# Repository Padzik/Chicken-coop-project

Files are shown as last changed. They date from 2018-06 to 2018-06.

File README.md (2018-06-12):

# Chicken coop project ("Kurník 21. století")
Chicken coop controller board (Eagle schematics) + arduino SW (for arduino and attiny + modified dependent libraries)

## HW comment
* Arduino nano + Attiny85 (for battery protection)
* LCD with nice user friendly menu
* External temp probe + automatic fan controller
* Set your GPS location (via menu) and you are ready to go! (actual Sunrise and Sunset is automaticly calculated every day + you can add user delay time)
* Build in Buzzer for Pavlov reflex (one minute before door open/close starts beeping)
* RTC has build in automatic SW correction (cheap RTCs can be running up to 30s late every day) + automatic summer/winter time
* External LED for door status + Data output via Serial 
* H-bridge + motor from screwdriver for door opening (build in safety mechanism for sensor failure) Door position is controlled by Magnetic Sensor Window Alarm Switch (I have tried mechanical and also Hall-sensor switches, but this one is more realible)
* It has also manual override function for doors
* Solar panel / main voltage power supply + UPS 6V battery (up to 2 days of running on battery backup) + Hibernation mode for low backup voltage on battery
* Double sided PCB can be easily prepared at home conditions (I have made many prototype versions)

Inspired by [Arduino chicken project by user RobotChicken](http://www.instructables.com/id/Arduino-Chicken-Coop-Controller/)

## Photos

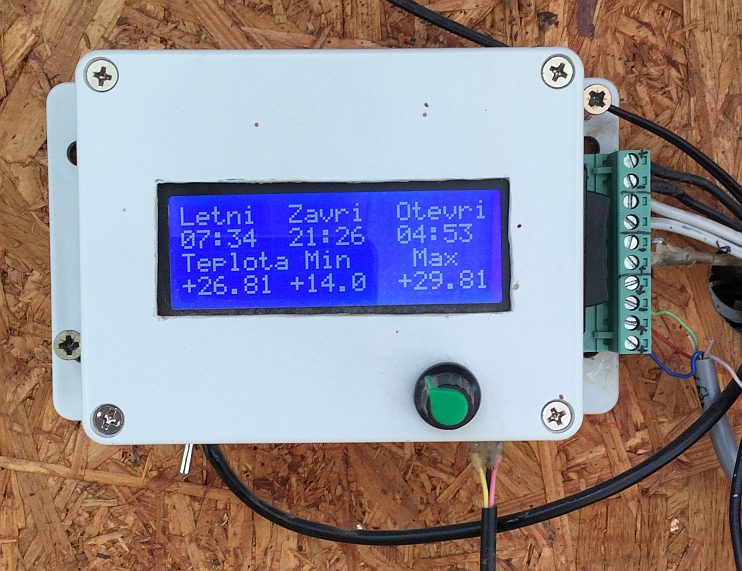
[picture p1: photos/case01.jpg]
Whole box


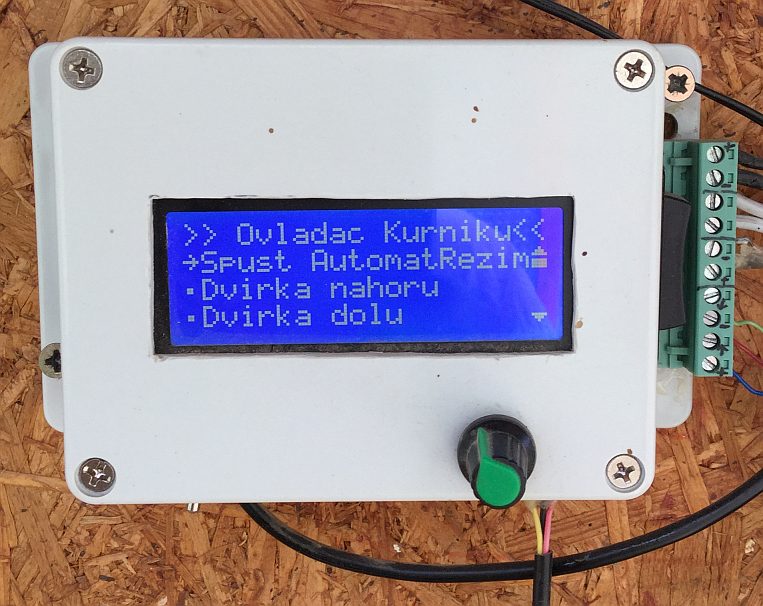
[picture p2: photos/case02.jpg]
Internal menu


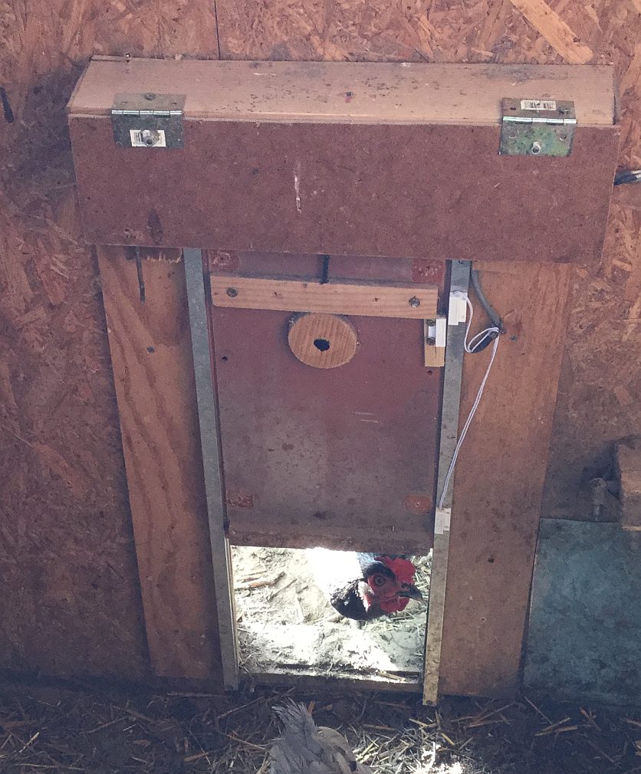
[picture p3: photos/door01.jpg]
Actual state of door HW


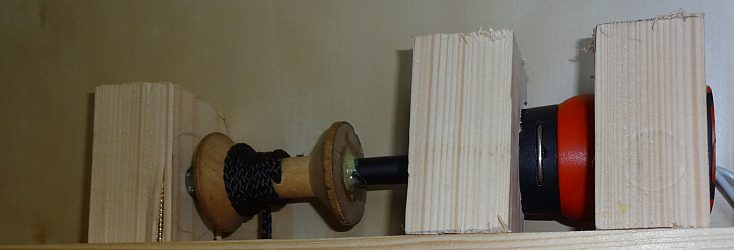
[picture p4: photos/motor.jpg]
Motor detail


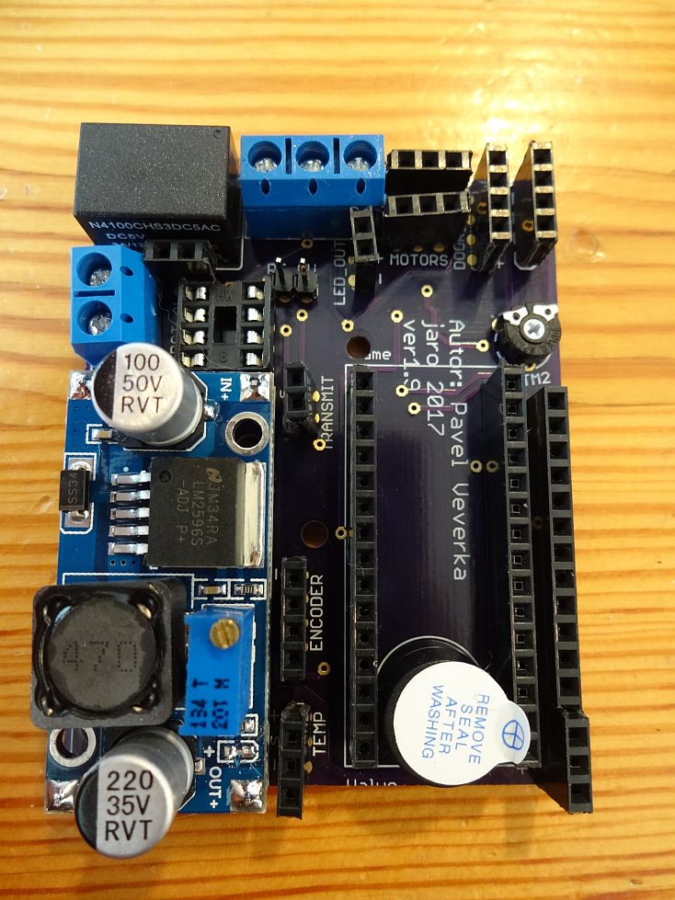
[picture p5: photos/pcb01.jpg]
PCB01


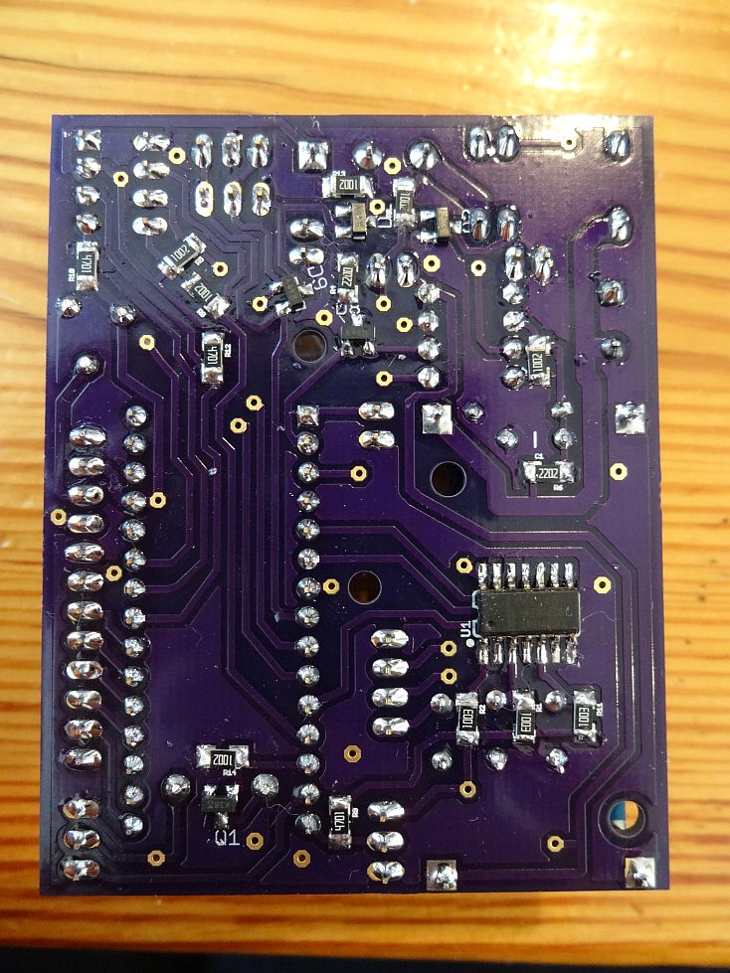
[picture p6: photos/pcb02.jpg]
PCB02


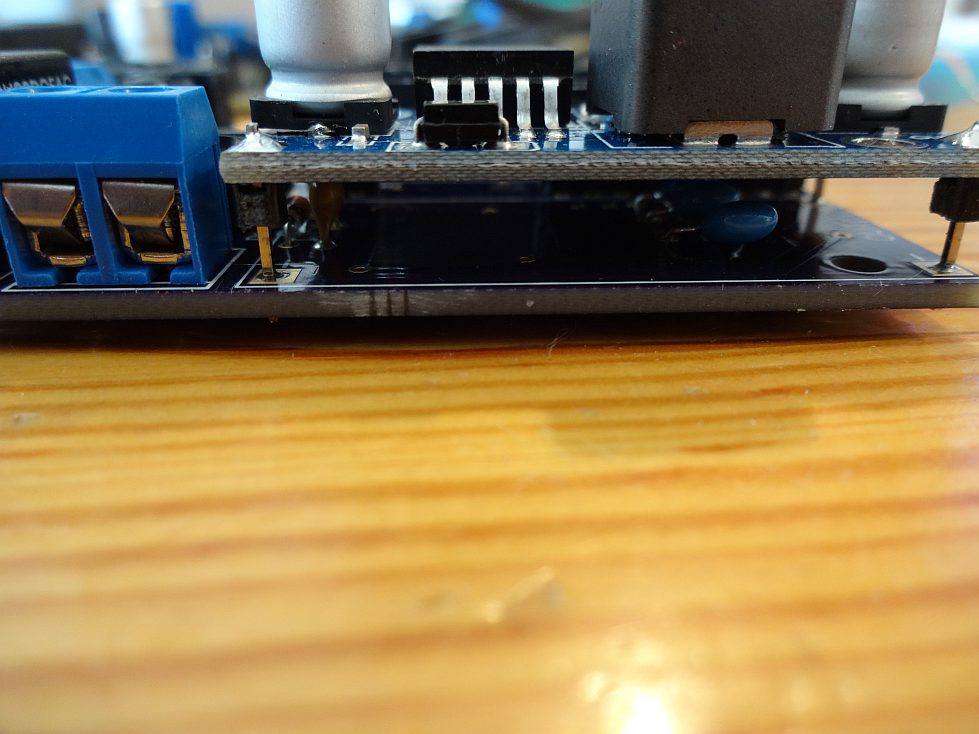
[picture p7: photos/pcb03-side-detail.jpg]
PCB03


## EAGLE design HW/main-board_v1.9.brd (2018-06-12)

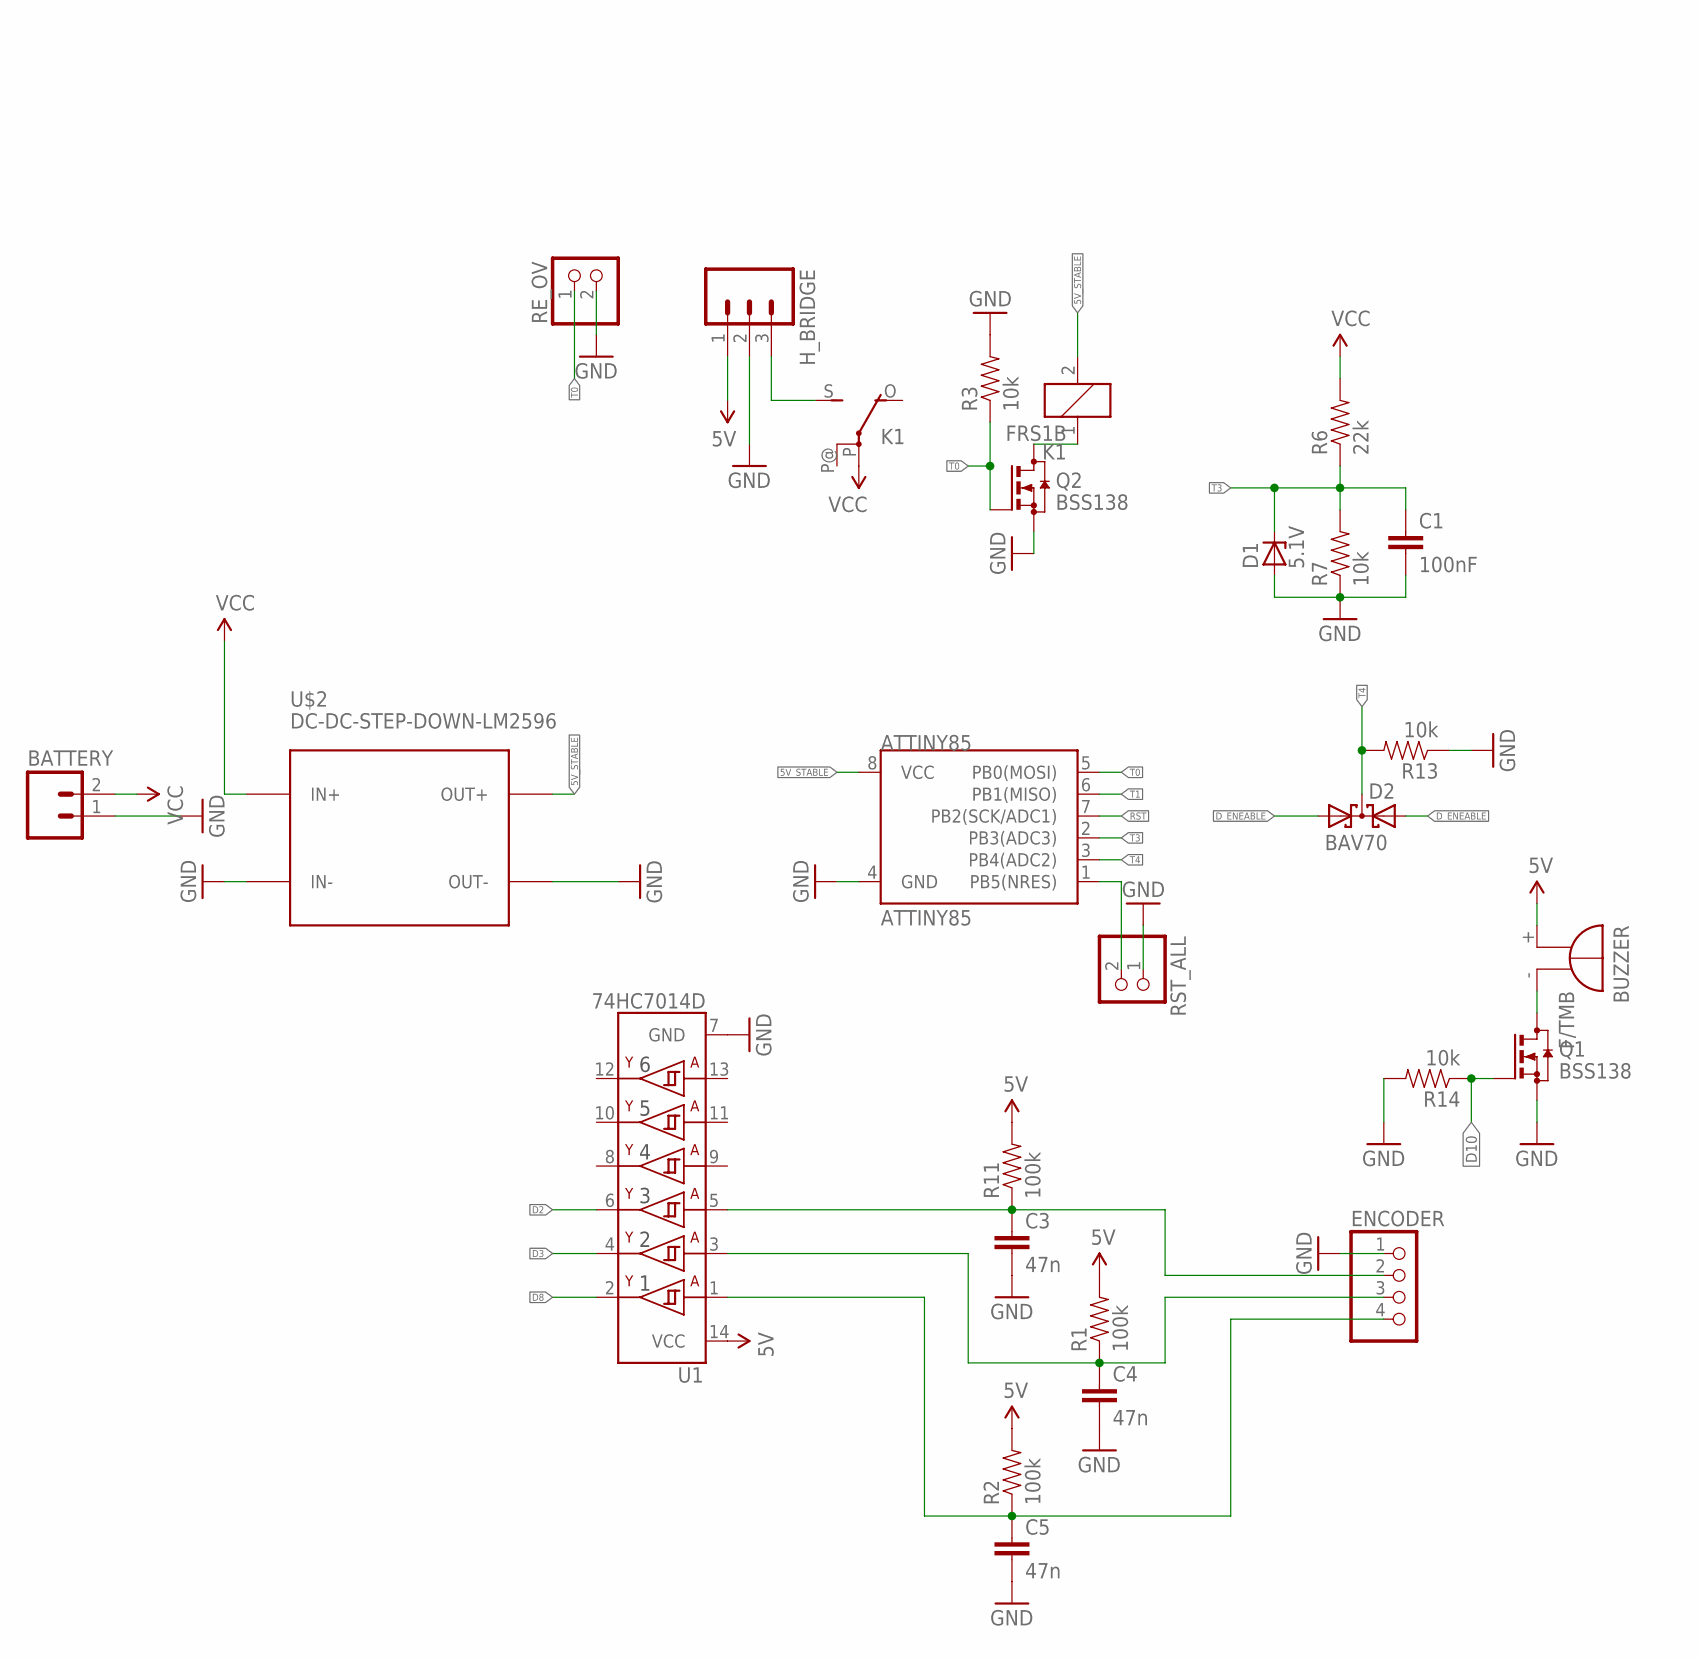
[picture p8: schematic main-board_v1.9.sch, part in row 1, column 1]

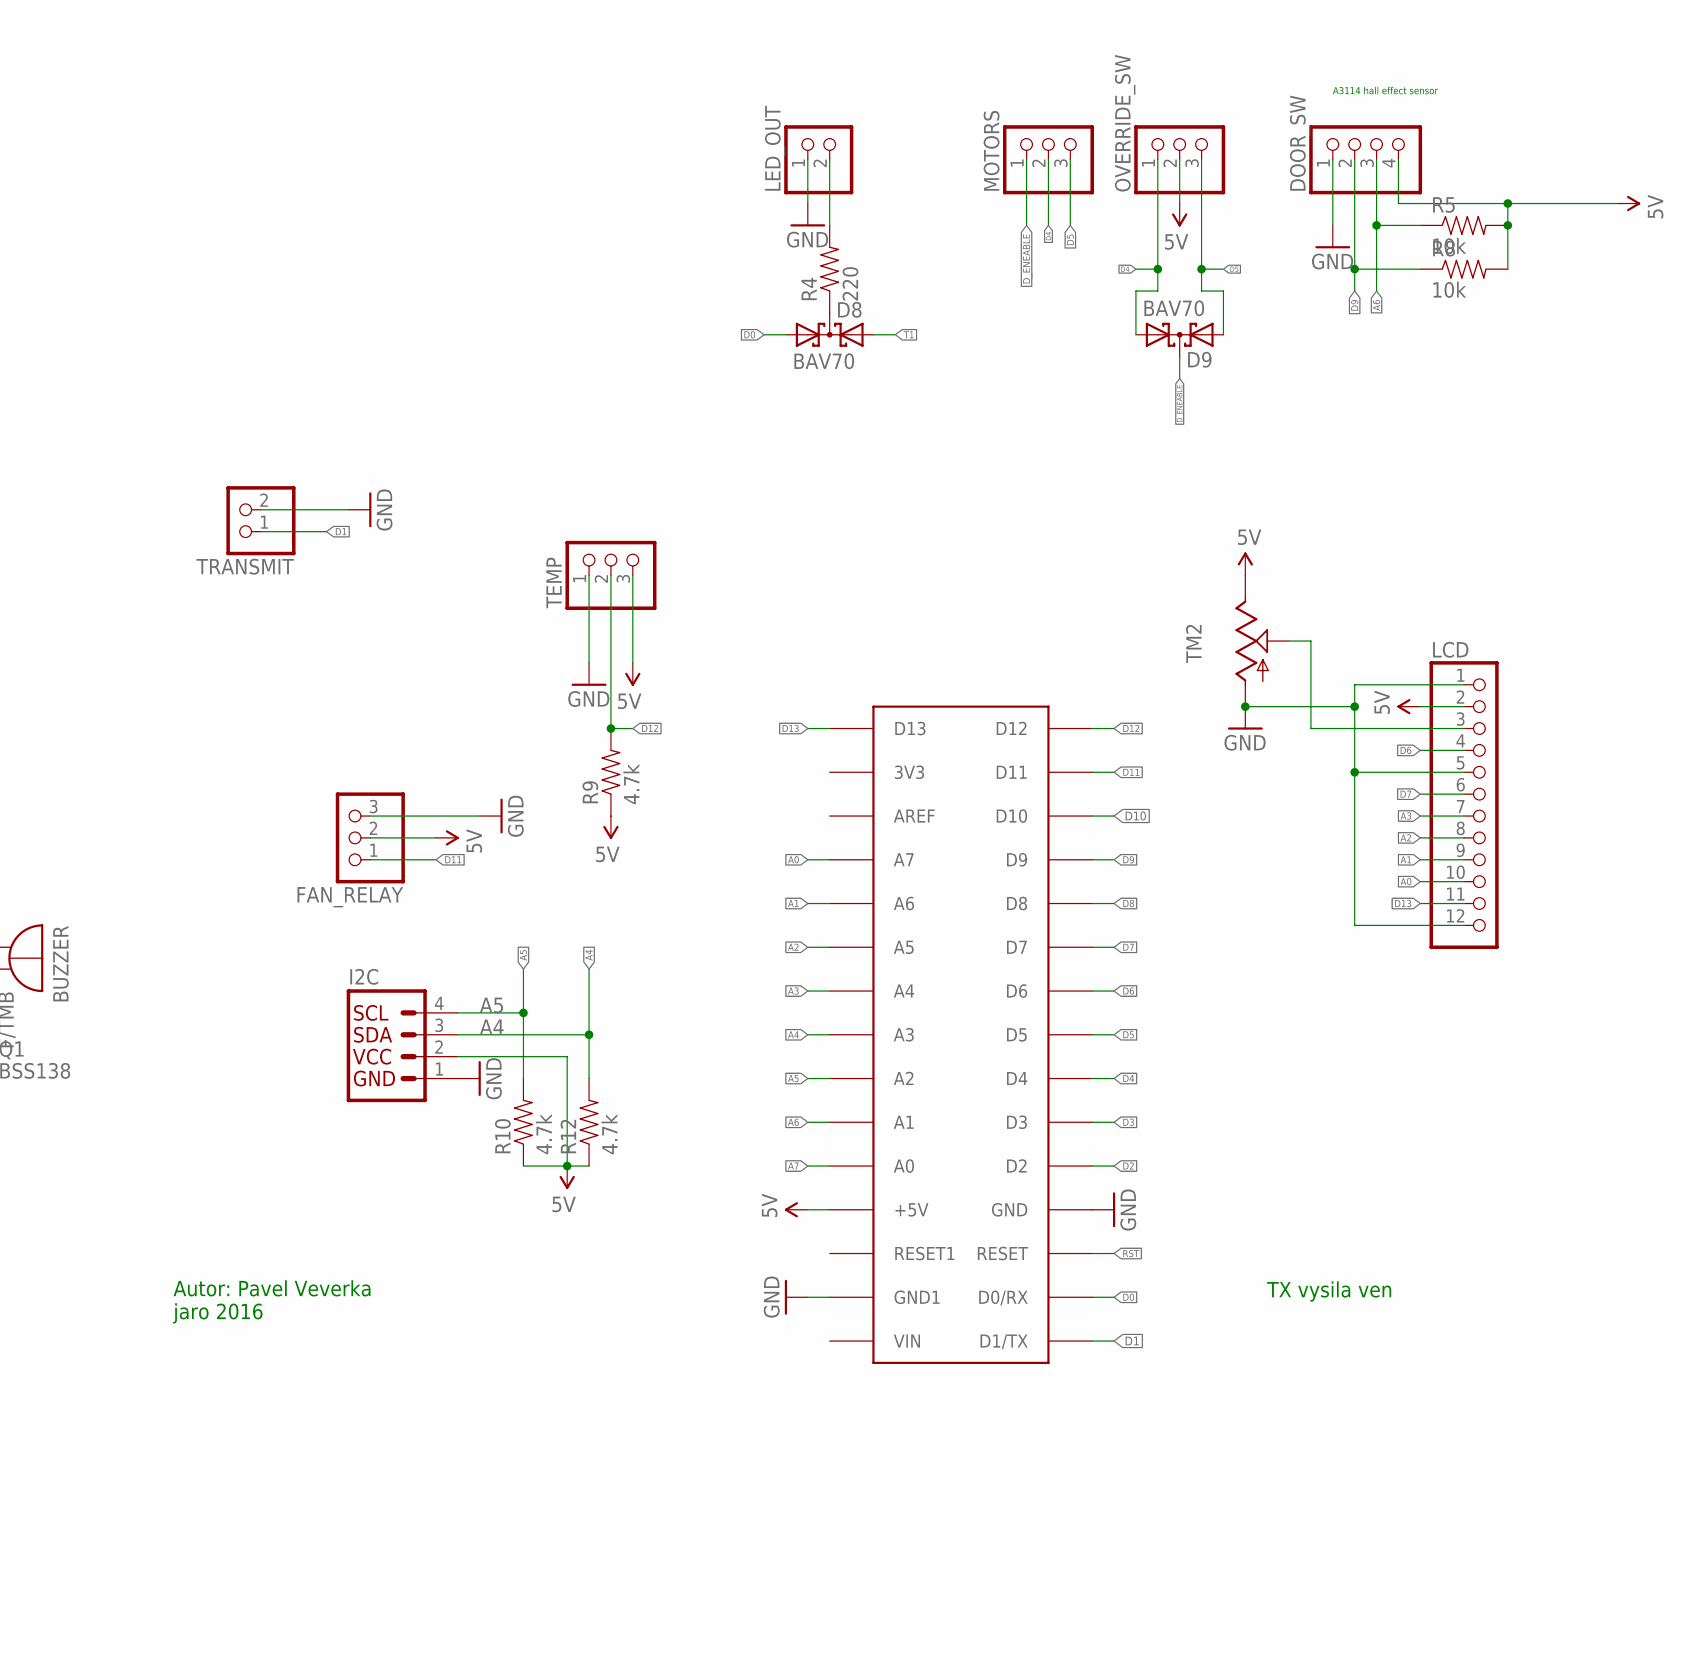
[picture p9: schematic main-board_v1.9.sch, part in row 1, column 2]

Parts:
ATTINY85: ATTINY85; DIP08
BATTERY: M025MM; SCREWTERMINAL-5MM-2
BUZZER: F/TMB
C1: 100nF; CAP-PTH-5MM
C3, C4, C5: 47n; CAP-PTH-5MM
D1: 5.1V; ZDIO-7.5
D2, D8, D9: BAV70; SOT23
DOOR_SW: PINHD-1X4; 1X04
ENCODER: PINHD-1X4; 1X04
FAN_RELAY: PINHD-1X3; 1X03
H_BRIDGE: M03-SCREW-5MM; SCREWTERMINAL-5MM-3
I2C: I2C_STANDARD; 1X04
K1: FRS1B
LCD: PINHD-1X12; 1X12
LED_OUT: PINHD-1X2; 1X02
MOTORS: PINHD-1X3; 1X03
NANO: NANO; PDIP-32
OVERRIDE_SW: PINHD-1X3; 1X03
Q1, Q2: BSS138; SOT23
R1, R2, R11: 100k; 1206
R3, R5, R7, R8, R13, R14: 10k; 1206
R4: 220; 1206
R6: 22k; 1206
R9, R10, R12: 4.7k; 1206
RE_OV: PINHD-1X2; 1X02
RST_ALL: PINHD-1X2; 1X02
TEMP: PINHD-1X3; 1X03
TM2: TRIM; 6MM
TRANSMIT: PINHD-1X2; 1X02
U1: 74HC7014D; SOIC-14
U$2: DC-DC-STEP-DOWN-LM2596

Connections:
5V: BUZZER.+, DOOR_SW.4, FAN_RELAY.2, H_BRIDGE.1, I2C.2, LCD.2, NANO.+5V, OVERRIDE_SW.2, R1.2, R2.2, R5.2, R8.2, R9.1, R10.1, R11.2, R12.1, TEMP.3, TM2.E, U1.14 (VCC)
5V_STABLE: ATTINY85.8 (VCC), K1.2, U$2.OUT+
A0: LCD.10, NANO.A7
A1: LCD.9, NANO.A6
A2: LCD.8, NANO.A5
A3: LCD.7, NANO.A4
A4: I2C.3, NANO.A3, R12.2
A5: I2C.4, NANO.A2, R10.2
A6: DOOR_SW.3, NANO.A1, R5.1
A7: NANO.A0
AS: C4.1, ENCODER.3, R1.1, U1.3 (2A)
ASDF: C5.1, ENCODER.4, R2.1, U1.1 (1A)
D0: D8.1 (A1), NANO.D0/RX
D1: NANO.D1/TX, TRANSMIT.1
D2: NANO.D2, U1.6 (3Y)
D3: NANO.D3, U1.4 (2Y)
D4: D9.1 (A1), MOTORS.2, NANO.D4, OVERRIDE_SW.1
D5: D9.2 (A2), MOTORS.3, NANO.D5, OVERRIDE_SW.3
D6: LCD.4, NANO.D6
D7: LCD.6, NANO.D7
D8: NANO.D8, U1.2 (1Y)
D9: DOOR_SW.2, NANO.D9, R8.1
D10: NANO.D10, Q1.1 (G), R14.1
D11: FAN_RELAY.1, NANO.D11
D12: NANO.D12, R9.2, TEMP.2
D13: LCD.11, NANO.D13
DS: C3.1, ENCODER.2, R11.1, U1.5 (3A)
D_ENEABLE: D2.2 (A2), D9.3 (C), MOTORS.1
GND: ATTINY85.4 (GND), BATTERY.1, C1.2, C3.2, C4.2, C5.2, D1.A, DOOR_SW.1, ENCODER.1, FAN_RELAY.3, H_BRIDGE.2, I2C.1, LCD.1, LCD.5, LCD.12, LED_OUT.1, NANO.GND, NANO.GND1, Q1.2 (S), Q2.2 (S), R3.2, R7.1, R13.1, R14.2, RE_OV.2, RST_ALL.1, TEMP.1, TM2.A, TRANSMIT.2, U1.7 (GND), U$2.IN-, U$2.OUT-
unnamed: ATTINY85.1 (PB5(NRES)), RST_ALL.2
unnamed: H_BRIDGE.3, K1.S
unnamed: D8.3 (C), R4.1
unnamed: K1.1, Q2.3 (D)
unnamed: LED_OUT.2, R4.2
unnamed: LCD.3, TM2.S
unnamed: BUZZER.-, Q1.3 (D)
RST: ATTINY85.7 (PB2(SCK/ADC1)), NANO.RESET
T0: ATTINY85.5 (PB0(MOSI)), Q2.1 (G), R3.1, RE_OV.1
T1: ATTINY85.6 (PB1(MISO)), D8.2 (A2)
T3: ATTINY85.2 (PB3(ADC3)), C1.1, D1.C, R6.1, R7.2
T4: ATTINY85.3 (PB4(ADC2)), D2.3 (C), R13.2
VCC: BATTERY.2, K1.P, R6.2, U$2.IN+

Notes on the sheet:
Autor: Pavel Veverka jaro 2016
TX vysila ven
A3114 hall effect sensor

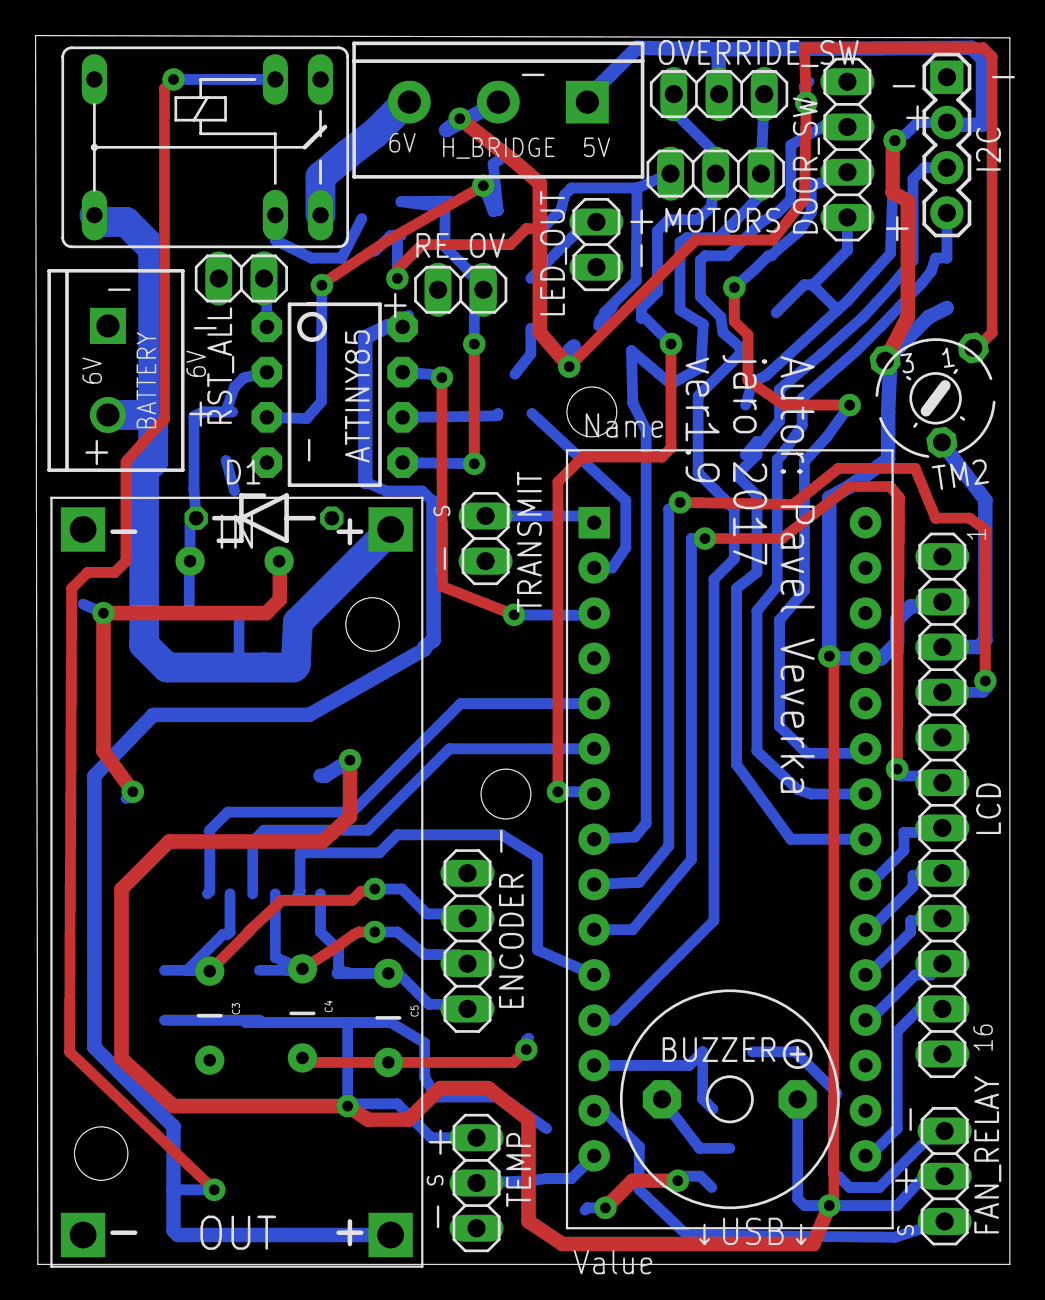
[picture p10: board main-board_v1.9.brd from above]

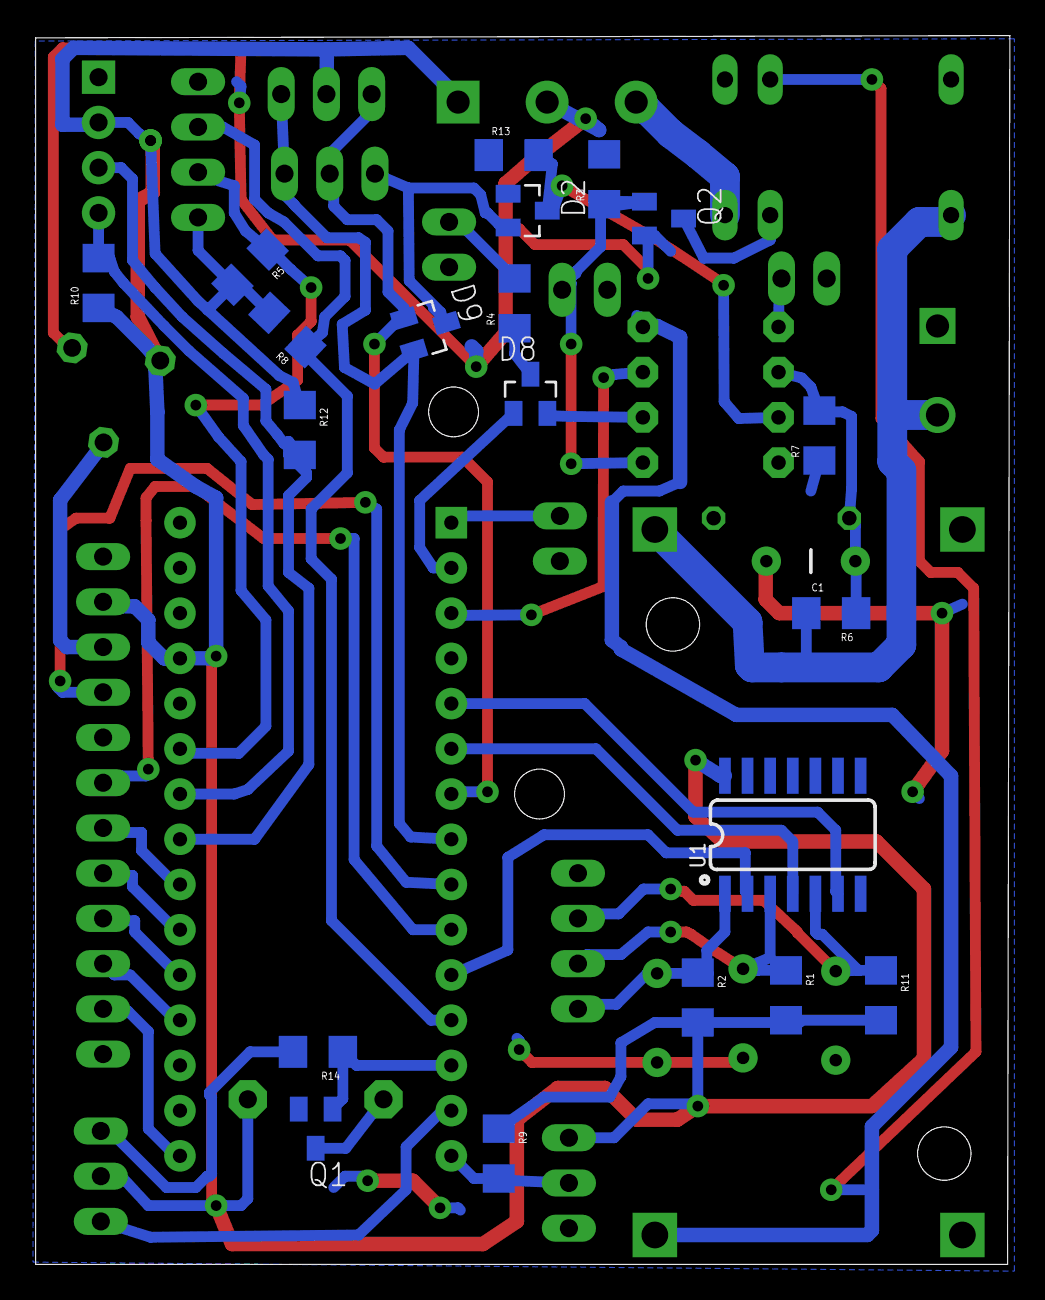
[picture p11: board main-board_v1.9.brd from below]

Board: 2 copper layers, 54.7 x 69.0 mm, 45 parts (21 on the bottom side), 41 nets.

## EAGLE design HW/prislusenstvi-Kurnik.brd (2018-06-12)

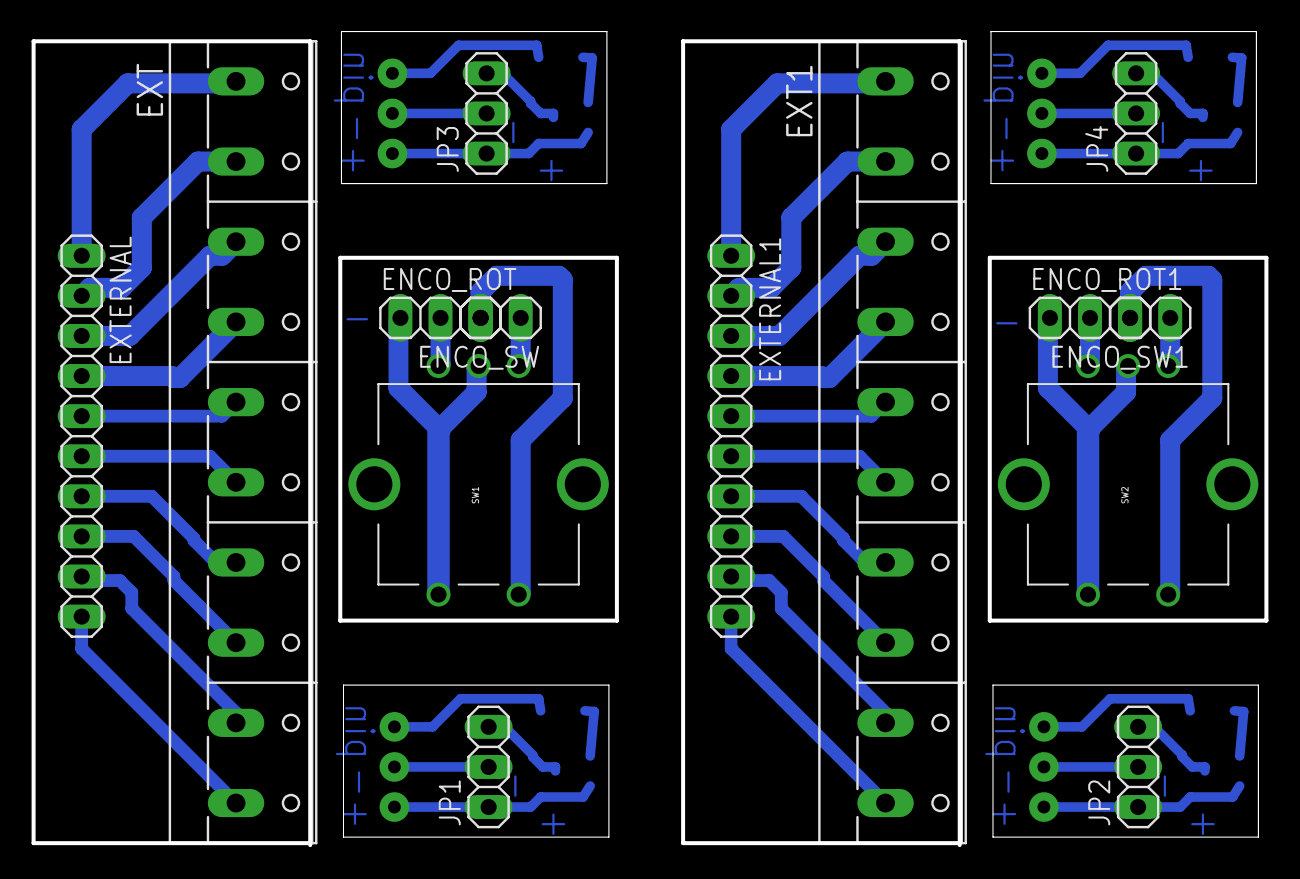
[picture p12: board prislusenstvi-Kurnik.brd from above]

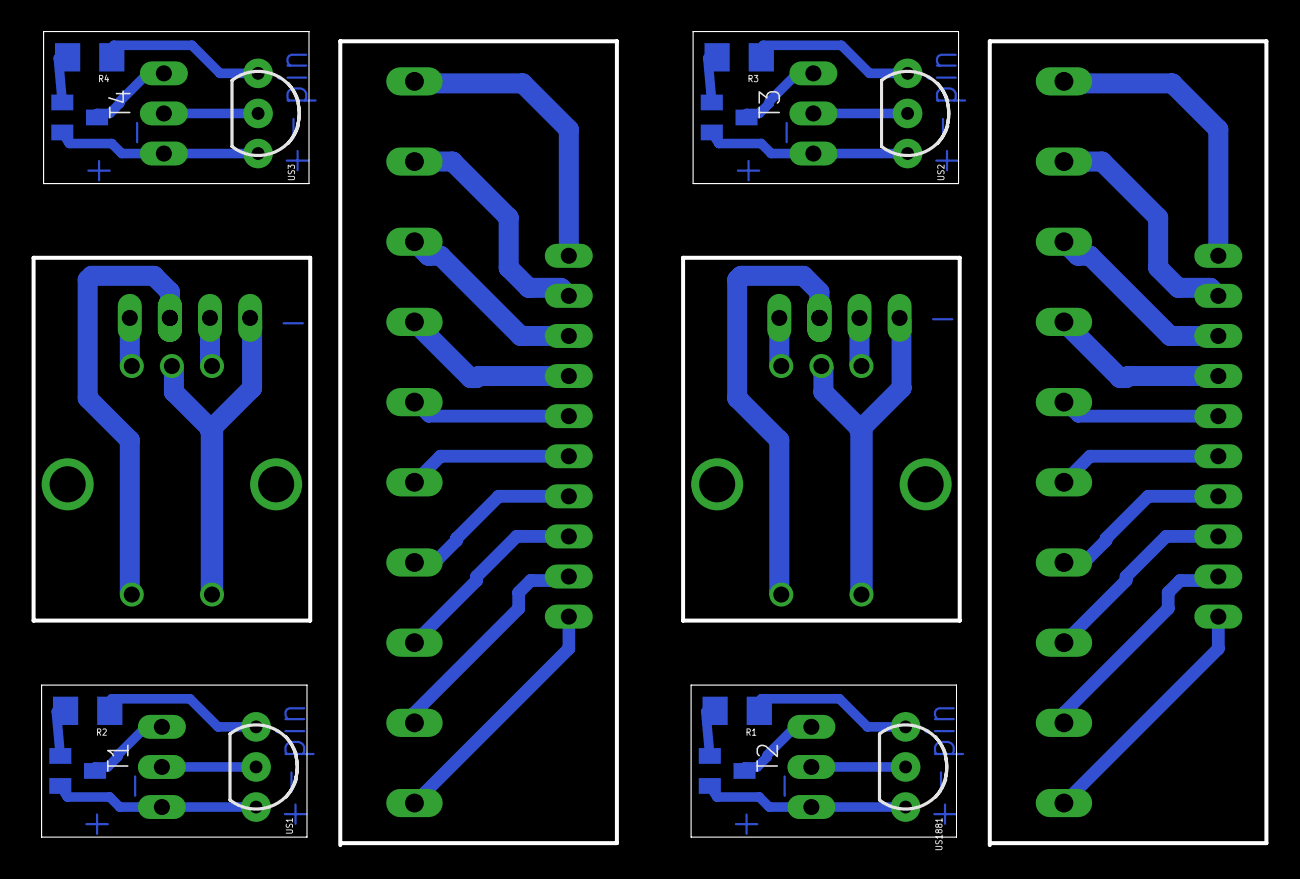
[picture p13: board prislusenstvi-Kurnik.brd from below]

Board: 2 copper layers, 78.1 x 51.5 mm, 26 parts (12 on the bottom side), 50 nets.

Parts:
ENCO_ROT, ENCO_ROT1: 1X03
ENCO_SW, ENCO_SW1: 1X02
EXT, EXT1: W237-10P
EXTERNAL, EXTERNAL1: 1X10
JP1, JP2, JP3, JP4: 1X03
R1, R2, R3, R4: 10k; 1206
SW1, SW2: ROTARTY_ENCODER; ROTARY_ENC_PLAIN
T1, T2, T3, T4: BC807-25; SOT23-BEC
US1, US2, US3, US1881: TO-92-AMMO

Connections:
5V: JP1.1, T2.E, US1881.3
5V1: JP2.1, T1.E, US1.3
5V2: JP3.1, T3.E, US2.3
5V3: JP4.1, T4.E, US3.3
E_BAT+: EXT.1, EXTERNAL.1
E_BAT+1: EXT1.1, EXTERNAL1.1
E_BAT-: EXT.2, EXTERNAL.2
E_BAT-1: EXT1.2, EXTERNAL1.2
E_DOOR1: EXT.7, EXTERNAL.7
E_DOOR2: EXT.8, EXTERNAL.8
E_DOOR3: EXT1.8, EXTERNAL1.8
E_DOOR4: EXT1.7, EXTERNAL1.7
E_GND: EXT.6, EXTERNAL.6
E_GND1: EXT1.6, EXTERNAL1.6
E_GND_T: EXT.10, EXTERNAL.10
E_GND_T1: EXT1.10, EXTERNAL1.10
E_LED+: EXT.5, EXTERNAL.5
E_LED+1: EXT1.5, EXTERNAL1.5
E_MOT+: EXT.3, EXTERNAL.3
E_MOT+1: EXT1.3, EXTERNAL1.3
E_MOT-: EXT.4, EXTERNAL.4
E_MOT-1: EXT1.4, EXTERNAL1.4
E_TEMP: EXT.9, EXTERNAL.9
E_TEMP1: EXT1.9, EXTERNAL1.9
GND: JP1.2, US1881.2
GND1: JP2.2, US1.2
GND2: JP3.2, US2.2
GND3: JP4.2, US3.2
unnamed: R1.2, T2.B
unnamed: R1.1, US1881.1
unnamed: ENCO_SW1.2, SW2.SW+
unnamed: ENCO_SW1.1, SW2.SW-
unnamed: R3.2, T3.B
unnamed: R3.1, US2.1
unnamed: ENCO_ROT1.2, SW2.C
unnamed: ENCO_ROT1.1, SW2.B
unnamed: ENCO_ROT1.3, SW2.A
unnamed: R2.2, T1.B
unnamed: R2.1, US1.1
unnamed: R4.2, T4.B
unnamed: R4.1, US3.1
unnamed: ENCO_SW.2, SW1.SW+
unnamed: ENCO_SW.1, SW1.SW-
unnamed: ENCO_ROT.2, SW1.C
unnamed: ENCO_ROT.1, SW1.B
unnamed: ENCO_ROT.3, SW1.A
PIN: JP1.3, T2.C
PIN1: JP2.3, T1.C
PIN2: JP3.3, T3.C
PIN3: JP4.3, T4.C

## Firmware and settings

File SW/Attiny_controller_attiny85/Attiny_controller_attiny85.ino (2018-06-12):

//pro attiny85

//5,7V na zdroji je dolni limit detekce
//graf spojnice trendu: y=0,3148x-0,0274


/* Spotreba: (mereno na verzi 1.8, 21/01/2017) (bez vetraku, na lab. zdroji)
 *  (6.77V)
 * vse v pohotovosti 114 mA
 * lcd vypnuto 91 mA
 *  (6.27V)
 * nouzovy rezim 14 mA, pri probrani attiny 23 mA
 * bazalni spotreba 5V stabilizatoru 10 mA
 * 
 * Baterka: 6V 4.5Ah
 * 91mA pri 6.5v -> 0.5915 W
 * 4.5Ah/0.091A=49.5h -> 2 dny a kousek
 * pri 60Ah 12V baterce tedy cca: 55 dni
 */



//#define INTERNAL2V56_NO_CAP (6)


#define RelayOn HIGH
#define RelayOff LOW

#define pin_Relay 0 //0
#define pin_LED 1 //1
#define pin_ArdRst 2
#define pin_MotIn 4
#define pin_BatteryIn A3


#include <avr/sleep.h>
#include <avr/wdt.h>
 
#ifndef cbi
#define cbi(sfr, bit) (_SFR_BYTE(sfr) &= ~_BV(bit))
#endif
#ifndef sbi
#define sbi(sfr, bit) (_SFR_BYTE(sfr) |= _BV(bit))
#endif


const float Vref = 4.99;  //4.99;            // Actual voltage and resistor values can be set here. 
const float R1 =  21900.0;            // R1 is nominally 22k
const float R2 =  10000.0;            // R2 is nominally 10k

const float resDiv = (R2/(R1 + R2));  // Resistor divider factor applied to measured voltage.
// resDiv = 0,31347

const float voltageLowSet = 6.35;             // Set low voltage threshold (engine off).
const float voltageHighSet = 6.7;            // Set high voltage threshold (engine running).

bool underVoltage = false, normal = true, wait_lowvoltage = false;
unsigned long motor_time = 0, wait_lowvoltage_time;
int motor_failsafe = 15;  //in seconds
int tim = 500;                         // Delay between low voltage checks
 

void setup() {
  pinMode(pin_Relay, OUTPUT);
  digitalWrite(pin_Relay, RelayOff);   
  pinMode(pin_LED, OUTPUT); 
  digitalWrite(pin_LED, LOW); 
  pinMode(pin_ArdRst, OUTPUT);
  digitalWrite(pin_ArdRst, HIGH);
  pinMode(pin_MotIn, INPUT); 
  pinMode(pin_BatteryIn, INPUT);

 setup_watchdog(7);                    // approximately 2 second sleep
 
  //blink on startup 
  for (int i=0; i<5; i++) {
    digitalWrite(pin_LED, HIGH);          
    delay(80);
    digitalWrite(pin_LED, LOW); 
    delay(80); 
  }  

 // This is the analogReference value for the ATTiny 2.56v internal
// reference, with no external cap bypass.
//  analogReference( INTERNAL2V56_NO_CAP );
 
 analogReference(DEFAULT);
 delay(500); //nachystani ADC 
}

void loop() {
    float volts=getVolts();

    if (volts < (voltageLowSet-0.1)){ //very low battery
      wait_lowvoltage=true;
      
      normal=false;
      underVoltage=true;
      system_sleep();
    }


    if(volts<(voltageLowSet-0.05)){
      wait_lowvoltage=true;
      
       underVoltage=true;
    }
    
    if(volts>=voltageHighSet){ //nabijecka pripojena
       underVoltage=false;
       normal=true;
       wait_lowvoltage=false;
    }  


    if((voltageLowSet<volts)&&(volts<voltageHighSet)){
       //v normalnim rozsahu na baterku
       wait_lowvoltage=false;
       if(underVoltage) { //jednou jsem tam, pozor. cekam na nabijecku
            //another measurement to ensure low voltage
            delay(100);
            if(volts<(getVolts()-0.05)){
              // delay(tim);
               normal=false;
              // system_sleep();
            }
       }
       else normal=true;   
    }


  
    if(underVoltage){ //safe mode
      if(wait_lowvoltage){
        wait_lowvoltage_time=millis()/1000; 
        if((millis()/1000-wait_lowvoltage_time)>=5){ //po 5s udelat nove mereni
                //reset arduino

              }    


        
      }
         digitalWrite(pin_Relay, RelayOff);
         for (int i=0; i<2; i++) {
            digitalWrite(pin_LED, HIGH);          
            delay(30);
            digitalWrite(pin_LED, LOW); 
            delay(30); 
          }    
      //usporny rezim a pauza do dalsiho mereni 60s

      system_sleep();
     // delay(tim);
    }
    else{ //normal mode    
      if(normal) digitalWrite(pin_Relay, RelayOn);
      
       if(digitalRead(pin_MotIn)){ //motor is running
          motor_time=millis()/1000; //in seconds
          do{
              if(digitalRead(pin_MotIn)==0) break;
              if((millis()/1000-motor_time)>=motor_failsafe){ //problem
                //reset arduino
                digitalWrite(pin_ArdRst, LOW);          
                delay(50);
                digitalWrite(pin_ArdRst, HIGH); 
                break;
              }
          }while(digitalRead(pin_MotIn)); 
       }
       wait_lowvoltage=false; 
     }
   
  delay(300);
}


float getVolts() {                    // Function returns the actual battery volts.
  int raw=0;
  raw = analogRead(pin_BatteryIn);
  float volts = (raw / 1023.0) * Vref;
  volts = (volts / resDiv)+0.08; //+ konstanta ziskana merenim
  return volts;
}  




// Put system into the sleep state
void system_sleep() {
  cbi(ADCSRA,ADEN);                    // switch ADC OFF to save power
 
  set_sleep_mode(SLEEP_MODE_PWR_DOWN); // sleep mode is set here
  sleep_enable();
  sleep_mode();                        // System sleeps here
 
  sleep_disable();                     // System continues execution here when watchdog times out
  sbi(ADCSRA,ADEN);                    // switch ADC back ON
}

// 0=16ms, 1=32ms,2=64ms,3=128ms,4=250ms,5=500ms
// 6=1 sec,7=2 sec, 8=4 sec, 9= 8sec
void setup_watchdog(int ii) {          // set the required register bits to
                                       // set up the watcdog timer.
  byte bb;
  if (ii > 9 ) ii=9;
  bb = ii & 7;
  if (ii > 7) bb |= (1<<5);
  bb |= (1<<WDCE);
 
  MCUSR &= ~(1<<WDRF);
  WDTCR |= (1<<WDCE) | (1<<WDE);
  WDTCR = bb;
  WDTCR |= _BV(WDIE);
}
 
// Watchdog Interrupt Service / is executed when watchdog times out
ISR(WDT_vect) {
 // Include this routine even if it doesn't do anything.
}

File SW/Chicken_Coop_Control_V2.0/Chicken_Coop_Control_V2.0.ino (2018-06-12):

//project based on code by Perry Childs
#define lcd_rows 4
#define lcd_columns 20

//relay fan changes
#define FANON LOW
#define FANOFF HIGH

// Encoder 1 returns U for up and D for down. phi_rotary_encoders my_encoder1(mapping1, Encoder1ChnA, Encoder1ChnB, Detent);
#define EncoderDetent 20
#define btn_u 8
#define btn_d 8
#define btn_l 8
#define btn_r 8
#define btn_b 8
#define btn_a 8
#define btn_null 0
#define total_buttons 6

// Arduino pin setting

#define Probe 12
#define pinFan 11
#define FLED 0 //z 4ky

#define pinIP1 4 //motor
#define pinIP2 5 //motor



#define Encoder1_SW 3
#define Encoder1ChnB 8
#define Encoder1ChnA 2 

#define LCD_RS 6
#define LCD_EN 7 
#define LCD_D4 A3
#define LCD_D5 A2
#define LCD_D6 A1
#define LCD_D7 A0

#define backLight 13 //5

//digital door input
//#define INVERTED_DOORS //odkomentovat pro nula=sepnuto
#define pinLiT 88 //door input //A6
#define pinLiB 9  //door input //D9

#define PIN_TX 1 
#define pinSpeaker 10

#include <Arduino.h>
#include <Wire.h>
#include <DS1307.h>
#include <OneWire.h>
#include <EEPROM.h>
#include <LCD.h>
#include <phi_interfaces.h>
#include <phi_prompt.h>
#include <Sunrise.h>
#include <SendOnlySoftwareSerial.h>




#define STOP 0
#define UP 1
#define DOWN -1
#define DoorDown 68
#define DoorUp 85
#define Overide 90
#define debounce_delay 150
#define NumKeys 5

#define BUTTON_UP 1
#define BUTTON_DOWN 2
#define BUTTON_SELECT 5

namespace butto{ 
  volatile int button_pressed;  
}


// Create hardware objects


LiquidCrystal lcd(LCD_RS,LCD_EN,LCD_D4,LCD_D5,LCD_D6,LCD_D7); // Create the lcd object 

int rtc[7];
OneWire TempProbe(Probe);
float Latitude, Longitude;
int TimeZone, Lat_pre, Lat_suf, Lon_pre, Lon_suf;
//Sunrise mySunrise(49.18,16.53,1);//Brno, CzechRep, Europe - Latitude/Longitude and Timezone 49.18N,16.53E: 	49.18,16.53, 1=time zone
Sunrise mySunrise(0,0,0); //create global variable, update values later
SendOnlySoftwareSerial mySerial (PIN_TX);  // Tx pin

// Global variables
int GlobTime, OldGlobTime, WakeTime, BedTime, Flash, stateMotor, door_action, toggle=HIGH, BST_flag; //odebrano adc_key_in, key=-1, oldkey=-1,
long GlobTimeSeconds, OldGlobTimeSeconds;
int AddRiseTime, AddSetTime; //correction for computed suset/rise time
//char buf[6];
int MaxTReading, MaxTSignBit, MinTReading, MinTSignBit, TReading, SignBit;
int isLcdLightOn = false;
//int adc_key_val[5] ={ 30, 150, 360, 535, 760 }; //zmena
//int UpRate;//=450; //puv 300
//int DownRate;//=220; //puv 200
int backLightTime; //z puvodnich 300
//int MotorFailSafe = 6; //z puvodnich 3 // kolik sekund se bude vytahovat
int MotorOnTime;
int SetFlashOn = false;
int ControllerRunning = false;
int FanTemp, ActualTemp;
int FanTime; //minutes to spin fan and than same pause
bool FanRun = false, AutoFan=false, mute, speaker_running=false;
int FanLastSpin=0; //zmena z unsigned long
bool NewDayTimeCorection = true; //was time corrected today?
int TimeCorection;// = 40; //seconds to substract
int LastDayCorection = -1;

int MotorFailSafeOpen;// = 7;
int MotorFailSafeClose;// = 4;


//fan symbol PROGMEM const 
const uint8_t fan_symbol[8]  = {0x0,0x6,0x14,0x1b,0x5,0xc,0x0};
const uint8_t fan_auto_symbol[8]  = {0x1f,0x0,0x6,0x14,0x1b,0x5,0xc};



//char mapping1[]={
//  'U','D'}; // This is a rotary encoder so it returns U for up and D for down on the dial.
//phi_rotary_encoders my_encoder1(mapping1, Encoder1ChnA, Encoder1ChnB, EncoderDetent);
char mapping[]={
  1,2,3,4,5,6}; // This is a list of names for each button.
byte pins[]={
  0,0,0,0,0,0}; // predposledni na nulu
phi_button_groups my_btns(mapping, pins, 6);
multiple_button_input * keypads[]={  &my_btns,0};
//&my_btns,&my_encoder1,0};

char up_keys[]={
  'U',0}; ///< All keys that act as the up key are listed here.
char down_keys[]={
  'D',0}; ///< All keys that act as the down key are listed here.
char left_keys[]={
  'U',0}; ///< All keys that act as the left key are listed here.
char right_keys[]={
  'D',0}; ///< All keys that act as the right key are listed here.
char enter_keys[]={
  5,0}; ///< All keys that act as the enter key are listed here.
char escape_keys[]={
  5,0}; ///< All keys that act as the escape key are listed here.
char * function_keys[]={
  up_keys,down_keys,left_keys,right_keys,enter_keys,escape_keys}; ///< All function key names are gathered here fhr phi_prompt.



PROGMEM const char msg_00[]="Navod k pouziti: v menu navigace koleckem a potvrzeni kliknutim. Nastavovani ciselnych polozek: toceni po smeru hodinovych rucicek cyklicky meni hodnotu, protismeru ulozi a klik preskoci zadavani.     Zprovoznil Pavel na zaklade navodu na webu od Perry Childs. Rijen 2014";

void setup()
{
  //dat najevo, ze funguje
  pinMode(backLight, OUTPUT);
  digitalWrite(backLight, HIGH);
//  delay(1000);

  
  lcd.begin(lcd_columns, lcd_rows);
  lcd.createChar(6, fan_symbol);
  lcd.createChar(7, fan_auto_symbol);
  init_phi_prompt(&lcd,keypads,function_keys, lcd_columns, lcd_rows, '~'); // Supply the liquid crystal object, input keypads, and function key names. Also supply the column and row of the lcd, and indicator as '>'. You can also use '\x7e', which is a right arrow.
//  init_phi_prompt(&lcd,0,0, lcd_columns, lcd_rows, '~'); // Supply the liquid crystal object, input keypads, and function key names. Also supply the column and row of the lcd, and indicator as '>'. You can also use '\x7e', which is a right arrow.
  
  coop_initialise();
}

void loop()
{
  top_menu();
}

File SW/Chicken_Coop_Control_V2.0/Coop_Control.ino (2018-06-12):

// Times are UK London revised on 1 Sep 2013
// Based on mid month times plus 15 mins to the nearest quarter hour - make sure you leave enough time for the chickens to go to bed - I left an addition 30mins after sunset

/*
int sun_set[24];
int sun_rise[24];
*/

//----------------------------------------------
// Start of Main Control Loop
//---------------------------------------------


void coop_initialise()
{   

   
  // Set pin modes
  pinMode(pinFan, OUTPUT);
  digitalWrite(pinFan, FANOFF);
  pinMode(pinIP1, OUTPUT);
  digitalWrite(pinIP1,LOW );
  pinMode(pinIP2, OUTPUT);
  digitalWrite(pinIP2,LOW);
  pinMode(FLED, OUTPUT);
  pinMode(pinSpeaker, OUTPUT);


  //dodelano
  pinMode(Encoder1ChnA, INPUT);  
  pinMode(Encoder1ChnB, INPUT);
  pinMode(Encoder1_SW, INPUT);

  attachInterrupt(0, encoderClick, RISING);
  attachInterrupt(1, buttonClick, RISING);

  

  //RTC_initialise(); //pak vypnout
  //Eeprom_init(); //run once

  
  
  LoadParameters(); //load from eeprom

  //loaded longitude + latitude from eeprom
  mySunrise.UpdateLocation(Latitude,Longitude,TimeZone);
  mySunrise.Actual();

  //Set initial state of the motors
  stateMotor= STOP;
  GlobTime = 0;
  CheckTempChange();

  

  mySerial.begin(9600);
  //mySerial.println("start");
  
  init_minutes();
  
  for(int k=0;k<3;k++){
    digitalWrite(FLED,HIGH);
    digitalWrite(pinSpeaker,HIGH);
    delay(150);
    digitalWrite(FLED,LOW);
    digitalWrite(pinSpeaker,LOW);
    delay(100);
  }
}



void run_controller()
{
  SetFlashOn=false;
  lcd.clear();
  get_time(); //nacita cas a blika
  OldGlobTimeSeconds=GlobTimeSeconds-1; //aby se po navratu z menu vypsal screen
  
  int LCDLightTimer=backLightTime;

  while (wait_on_escape(750)==0)
  {
    ControllerRunning = true;
    if (SetFlashOn==true) FlashLED();

    get_time(); //nacita cas a blika

    if(OldGlobTimeSeconds<=(GlobTimeSeconds-1)){ //one second tick
      OldGlobTimeSeconds=GlobTimeSeconds;

      //refresh LCD screen once in second
      lcd.setCursor(6,0);
      if(FanRun) lcd.write((uint8_t)6); //when spinning
      else if (AutoFan && Flash) lcd.write((uint8_t)7); //fan auto waiting symbol
      else lcd.print(" ");
      
      lcd.setCursor(7,0);
      lcd.print("Zavri  Otevri");
      //lcd.setCursor(0,1);
      print_time(); //tiskne cas
      print_door_time();
      lcd.setCursor(0,2);
      lcd.print("Teplota Min    Max");
      print_max_min_temp();
      print_current_temp();
    }
    
    

  
    if (WakeTime==GlobTime)door_change(DoorUp);
    if (BedTime==GlobTime) door_change(DoorDown);
    
    if (((WakeTime-1)==GlobTime) || ((BedTime-1)==GlobTime)){
      if(!mute && !Flash) digitalWrite(pinSpeaker, HIGH);
      else digitalWrite(pinSpeaker, LOW);
    } 

      
    if ((GlobTime==0) && (millis() > 70000 ) && (NewDayTimeCorection==true)) //0 minutes+running longer
      NewDayTimeCorection=false; //new day - needed new corection
    if (NewDayTimeCorection==false) RTC_correction(); //check seconds and correct  



    if(OldGlobTime<=(GlobTime-1)){ //one minute tick
      OldGlobTime=GlobTime;
      sendData(); //data serial logging
    }
    

    MotorOnTime = rtc[0];

    if (AutoFan) checkFan();

    while (stateMotor != STOP)
    {
      RTC.get(rtc,true);

      if (rtc[0]>=(MotorOnTime+MotorFailSafeClose))
        door_change(Overide);

      else
        door_change(0);
    }

    if(LCDLightTimer==0)
      digitalWrite(backLight, LOW);
      //lcd.noBacklight();
    LCDLightTimer--;
  }
}

//--------------------------------------------------
// End of Main Control Loop
//--------------------------------------------------


//--------------------------------------------------
// printing and setting the Sunrise and Sunset times
//--------------------------------------------------



void print_door_time()
{
  lcd.setCursor(7,1);
 // RTC.get(rtc,true);

  if(BedTime/60 < 10)
    lcd.print('0');  
  lcd.print(BedTime/60);
  lcd.print(":");
  if(BedTime%60 < 10)
    lcd.print('0');  
  lcd.print(BedTime%60);

  lcd.setCursor(14,1);
  //RTC.get(rtc,true);

  if(WakeTime/60 < 10)
    lcd.print('0');  
  lcd.print(WakeTime/60);
  lcd.print(":");
  if(WakeTime%60 < 10)
    lcd.print('0');  
  lcd.print(WakeTime%60);

}

////////////////////////////////////
// Set time in minutes to add to computed time of sunrise and sunset
///////////////////////////////////

void set_door_time()
{
  lcd.clear();
  lcd.print("Ranni cas dvirek + (min)");
  
  int user_input=AddRiseTime;
  phi_prompt_struct myIntegerInput;
  myIntegerInput.ptr.i_buffer=&user_input;
  myIntegerInput.low.i=0;
  myIntegerInput.high.i=200;
  myIntegerInput.step.i=5;
  myIntegerInput.col=10;
  myIntegerInput.row=2;
  myIntegerInput.width=3;
  myIntegerInput.option=1;
  input_integer(&myIntegerInput);
  AddRiseTime=user_input;   
  if(EEPROM_readInt(24)!=user_input) EEPROM_writeInt(24,user_input); //update eeprom

  lcd.clear();

  lcd.print("Vecerni cas dvirek + (min)");
  user_input=AddSetTime;
  //phi_prompt_struct myIntegerInput;
  myIntegerInput.ptr.i_buffer=&user_input;
  myIntegerInput.low.i=0;
  myIntegerInput.high.i=120;
  myIntegerInput.step.i=5;
  myIntegerInput.col=10;
  myIntegerInput.row=2;
  myIntegerInput.width=3;
  myIntegerInput.option=1;
  input_integer(&myIntegerInput);
  AddSetTime=user_input;   
  if(EEPROM_readInt(28)!=user_input) EEPROM_writeInt(28,user_input); //update eeprom

  
  wait_on_escape(2000);

}



//----------------------------------------------
// Door change and set 
// the State Motor variable to Stop
//---------------------------------------------
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

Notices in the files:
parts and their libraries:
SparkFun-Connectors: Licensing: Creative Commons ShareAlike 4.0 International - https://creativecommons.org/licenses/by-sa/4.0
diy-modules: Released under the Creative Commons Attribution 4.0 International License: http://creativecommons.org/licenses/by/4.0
